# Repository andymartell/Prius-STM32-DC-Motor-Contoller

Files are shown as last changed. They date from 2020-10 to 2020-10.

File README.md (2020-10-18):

# Prius-STM32-DC-Motor-Contoller

18/10/20  Updated the following:

- corrected tracking error around MG1 and MG2 current sensors.  J7 footprint updated (J1 left unchanged as tracking layout is currently ok).
- updated file names to remove spaces
- removed SG3204 and TX4313 -5V charge pumps and added LM2776 in their place in line with Jack Bauers latest updates

17/10/20  Initial release of files for manufacture.  
There are issues with these files, so use at your own risk.  
An updated version will follow once initial testing is complete!

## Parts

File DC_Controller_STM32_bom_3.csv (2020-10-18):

Component | Description | Part | References | Value | Footprint | Quantity Per PCB | Datasheet | JLPCB Component | JLPCB Extended | Mouser Part Number | Manufacturer_Name | Height | Mouser Price/Stock | Manufacturer_Part_Number | Arrow Part Number
1 | Unpolarized capacitor | C | C6 C7 C8 C11 C13 C16 C17 C18 C19 C25 C28 C32 C33 C34 C37 C38 C39 C41 C44 C45 C46 C47 C48 | 100nF | C_0603_1608Metric | 23 | ~ | C14663
2 | Unpolarized capacitor | C | C23 | 100uF | CP_EIA-3528-21_Kemet-B | 1 | ~ | C16133
3 | Polarized capacitor | CP | C61 C63 C64 C65 | 100uF | CP_EIA-3528-21_Kemet-B | 4 | ~ | C16133
4 | Unpolarized capacitor | C | C57 C75 C77 | 10uF | C_0805_2012Metric | 3 | ~ | C15850
5 | Unpolarized capacitor | C | C62 | 1n5 | C_0805_2012Metric | 1 | ~ | C1717
6 | Unpolarized capacitor | C | C9 C14 C20 C69 C70 C71 C72 | 1nF | C_0603_1608Metric | 7 | ~ | C1588
7 | Unpolarized capacitor | C | C1 C2 C4 C5 C10 C21 C26 C29 C30 C49 C54 C58 C67 C68 C76 | 1uF | C_0603_1608Metric | 15 | ~ | C15849
8 | Unpolarized capacitor | C | C74 | 1uF | C_0805_2012Metric | 1 | ~ | C15849
9 | Unpolarized capacitor | C | C12 C15 C35 C36 C40 C42 C43 | 20pF | C_0603_1608Metric | 7 | ~ | C1648
10 | Unpolarized capacitor | C | C27 C31 C53 | 22nf | C_0603_1608Metric | 3 | ~ | C21122
11 | Unpolarized capacitor | C | C59 | 22uF | C_0805_2012Metric | 1 | ~ | C45783
12 | Polarized capacitor | CP | C60 C66 | 330uF | CP_Elec_10x10 | 2 | ~ | C134522 | e
13 | Unpolarized capacitor | C | C55 | 33pF | C_0603_1608Metric | 1 | ~ | C1663
14 | Unpolarized capacitor | C | C3 C56 C73 | 4.7uF | C_0805_2012Metric | 3 | ~ | C1779
15 | Unpolarized capacitor | C | C22 C24 | 47n | C_0603_1608Metric | 2 | ~ | C1622
16 | 75V 0.15A Fast Switching Diode, SOD-123 | 1N4148W | D2 D5 D6 D7 D8 D9 D10 | 1N4148WS | D_SOD-323 | 7 | https://www.vishay.com/docs/85748/1n4148w.pdf | C2128
17 | Light emitting diode | LED | D1 D3 D4 D14 | LED | LED_0805_2012Metric | 4 | ~ | C84256
18 | Diode | D | D11 | SS54B | D_SMA | 1 | ~ | C22452
19 | Schottky diode | D_Schottky | D12 D13 | SS54B | D_SMA | 2 | ~ | C22452
20 | JST (JAPAN SOLDERLESS TERMINALS) - BM02B-CPTK-1A-TB - CONNECTOR, HEADER, 2POS, 1ROW, 2MM | BM02B-CPTK-1A-TB | J5 | BM02B-CPTK-1A-TB | BM02BCPTK1ATB | 1 | http://www.jst-mfg.com/product/pdf/eng/eCPT.pdf |  |  | 306-BM02B-CPTK-1A-TB | JST (JAPAN SOLDERLESS TERMINALS) | 11.7 | https://www.mouser.co.uk/ProductDetail/JST-Automotive/BM02B-CPTK-1A-TB?qs=XoGB3caz5%2FYlNzGrdhaY5g%3D%3D | BM02B-CPTK-1A-TB
21 | Header Top 8 Double CPT | BM08B-CPTK-1A-TB | J8 | BM08B-CPTK-1A-TB | BM08BCPTK1ATB | 1 | http://www.jst-mfg.com/product/pdf/eng/eCPT.pdf |  |  | 306-BM08B-CPTK-1A-TB | JST (JAPAN SOLDERLESS TERMINALS) | 12 | https://www.mouser.co.uk/ProductDetail/JST-Automotive/BM08B-CPTK-1A-TB?qs=XoGB3caz5%2FYvSzPNYjsAKw%3D%3D | BM08B-CPTK-1A-TB
22 | Top Entry disconnectable, crimp style Shrouded Header, 50 positions | BM50B-SHLDS-G-TFT | J6 | BM50B-SHLDS-G-TFT | BM50BSHLDSGTFT | 1 | http://www.jst-mfg.com/product/pdf/eng/eSHLD.pdf |  |  |  | JST (JAPAN SOLDERLESS TERMINALS) | 4.05 |  | BM50B-SHLDS-G-TFT
23 | Generic connector, single row, 01x02, script generated (kicad-library-utils/schlib/autogen/connector/) | Conn_01x02 | J13 J19 | Conn_01x02 | PinHeader_1x02_P2.54mm_Vertical | 2 | ~
24 | Generic connector, single row, 01x03, script generated (kicad-library-utils/schlib/autogen/connector/) | Conn_01x03 | J12 | Conn_01x03 | PinHeader_1x03_P2.54mm_Vertical | 1 | ~
25 | Generic connector, single row, 01x04, script generated (kicad-library-utils/schlib/autogen/connector/) | Conn_01x04 | J4 J10 J17 | Conn_01x04 | PinHeader_1x04_P2.54mm_Vertical | 3 | ~
26 | Generic connector, single row, 01x06, script generated (kicad-library-utils/schlib/autogen/connector/) | Conn_01x06 | J15 | Conn_01x06 | PinHeader_1x06_P2.54mm_Vertical | 1 | ~
27 | Generic connector, double row, 02x05, odd/even pin numbering scheme (row 1 odd numbers, row 2 even numbers), script generated (kicad-library-utils/schlib/autogen/connector/) | Conn_02x05_Odd_Even | J14 | Conn_02x05_Odd_Even | PinHeader_2x05_P2.54mm_Vertical | 1 | ~
28 | Generic connector, double row, 02x05, odd/even pin numbering scheme (row 1 odd numbers, row 2 even numbers), script generated (kicad-library-utils/schlib/autogen/connector/) | Conn_02x05_Odd_Even | J9 | Conn_02x05_Odd_Even | PinHeader_2x05_P2.54mm_Horizontal | 1 | ~
29 | Generic connector, double row, 02x06, odd/even pin numbering scheme (row 1 odd numbers, row 2 even numbers), script generated (kicad-library-utils/schlib/autogen/connector/) | Conn_02x06_Odd_Even | J11 | Conn_02x06_Odd_Even | PinHeader_2x06_P2.54mm_Vertical | 1 | ~
30 | Generic connector, double row, 02x20, odd/even pin numbering scheme (row 1 odd numbers, row 2 even numbers), script generated (kicad-library-utils/schlib/autogen/connector/) | Conn_02x20_Odd_Even | J2 | Conn_02x20_Odd_Even | IDC-Header_2x20_P2.54mm_Horizontal | 1 | ~
31 | JST (JAPAN SOLDERLESS TERMINALS) - SM02B-CPTK-1A-TB - CONNECTOR, HEADER, 2POS, 1ROW, 2MM | SM02B-CPTK-1A-TB | J3 | SM02B-CPTK-1A-TB | SM02BCPTK1ATB | 1 | https://www.jst.co.uk/downloads/series/eCPT_(15-08-31).pdf |  |  | 306-SM02B-CPTK-1A-TB | JST (JAPAN SOLDERLESS TERMINALS) | 6.8 | https://www.mouser.co.uk/ProductDetail/JST-Automotive/SM02B-CPTK-1A-TB?qs=XoGB3caz5%2FZTJkgXMJqmuw%3D%3D | SM02B-CPTK-1A-TB
32 | Automotive Connectors SIDE ENTRY CPT HDR 2.0MM PITCH | SM08B-CPTK-1A-TBL | J7 | SM08B-CPTK-1A-TB | SM08BCPTK1ATBL_odd_even | 1 | http://www.jst-mfg.com/product/pdf/eng/eCPT.pdf |  |  |  | JST (JAPAN SOLDERLESS TERMINALS) | 12 |  | SM08B-CPTK-1A-TB
33 | Automotive Connectors SIDE ENTRY CPT HDR 2.0MM PITCH | SM08B-CPTK-1A-TBL | J1 | SM08B-CPTK-1A-TBL | SM08BCPTK1ATBL | 1 | http://www.jst-mfg.com/product/pdf/eng/eCPT.pdf |  |  | 306-SM08B-CPTK-1ATBL | JST (JAPAN SOLDERLESS TERMINALS) | 9.3 | https://www.mouser.co.uk/ProductDetail/JST-Automotive/SM08B-CPTK-1A-TBL?qs=XoGB3caz5%2FYptClYcBhvSw%3D%3D | SM08B-CPTK-1A-TBL
34 | CABLE TAG-CONNECT IN-CIRCUIT LEG | TC2030-MCP | J16 J18 | TC2030-MCP | TC2030MCP | 2 | http://www.tag-connect.com/Materials/TC2030-MCP%20Datasheet.pdf |  |  |  | Tag Connect | 18.669 |  | TC2030-MCP | TC2030-MCP
35 | Inductor, small symbol | L_Small | L2 L3 | 10uH | L_0805_2012Metric | 2 | ~ | C1046 | e
36 | Inductor | L | L4 | 220uH | L_12x12mm_H6mm | 1 | ~ | C169402 | e
37 | Inductor | L | L1 | 4.7uH | L_1210_3225Metric | 1 | ~ | C76842 | e
38 | 0.2A Ic, 40V Vce, Small Signal NPN Transistor, SOT-23 | MMBT3904 | Q2 Q10 Q11 Q12 Q13 Q14 Q15 Q16 Q17 Q18 Q19 Q20 Q21 Q22 Q23 Q24 Q25 | MMBT3904 | SOT-23 | 17 | https://www.fairchildsemi.com/datasheets/2N/2N3904.pdf | C20526
39 | N-MOSFET transistor, gate/drain/source, drain connected to mounting plane | Q_NMOS_GDSD | Q1 Q5 Q6 Q7 Q8 Q9 | NCV8402A | SOT-223 | 6 | ~ | C77755 | e
40 | NPN transistor, base/emitter/collector | Q_NPN_BEC | Q3 Q4 | S8050 | SOT-23 | 2 | ~ | C2146
41 | Resistor | R | R103 | 0.22R | R_0805_2012Metric | 1 | ~ | C36234 | e
42 | Resistor | R | R12 R15 R17 R93 R98 R106 R107 R121 R125 | 0R | R_0603_1608Metric | 9 | ~ | C21189
43 | Resistor | R | R37 | 1.2k | R_0603_1608Metric | 1 | ~ | C22765
44 | Resistor | R | R10 R11 R16 R19 R30 R109 R112 | 1.5k | R_0603_1608Metric | 7 | ~ | C22843
45 | Resistor | R | R54 R57 R58 R61 R62 R64 R66 R68 R70 R72 R74 R76 R78 R80 | 100R | R_0603_1608Metric | 14 | ~ | C22775
46 | Resistor | R | R87 R88 R89 R101 | 100k | R_0603_1608Metric | 4 | ~ | C25803
47 | Resistor | R | R2 R7 R22 R23 R29 R32 R35 R38 R39 R41 R43 R52 R81 R91 R97 | 10k | R_0603_1608Metric | 15 | ~ | C25804
48 | Resistor | R | R83 | 120R | R_0603_1608Metric | 1 | ~ | C22787
49 | Resistor | R | R102 | 180R | R_0603_1608Metric | 1 | ~ | C22828
50 | Resistor | R | R26 | 182k | R_0805_2012Metric | 1 | ~
51 | Resistor | R | R21 R42 R44 R46 R49 R50 R53 R55 R56 R59 R60 R63 R65 R67 R69 R71 R73 R75 R77 R79 R82 R84 R85 R92 R96 R126 | 1k | R_0603_1608Metric | 26 | ~ | C21190
52 | Resistor | R | R5 R40 R48 | 2.2k | R_0603_1608Metric | 3 | ~ | C4190
53 | Resistor | R | R105 | 2.4k | R_0603_1608Metric | 1 | ~ | C22940
54 | Resistor | R | R108 | 2.7k | R_0603_1608Metric | 1 | ~ | C13167
55 | Resistor | R | R45 R47 R110 | 22k | R_0603_1608Metric | 3 | ~ | C31850
56 | Resistor | R | R34 R36 | 3.3k | R_0603_1608Metric | 2 | ~ | C22978
57 | Resistor | R | R117 R118 R119 R120 | 3.6k | R_0603_1608Metric | 4 | ~ | C22980
58 | Resistor | R | R31 | 3.9k | R_0603_1608Metric | 1 | ~ | C23018
59 | Resistor | R | R95 | 330R | R_0603_1608Metric | 1 | ~ | C23138
60 | Resistor | R | R27 | 392k | R_0805_2012Metric | 1 | ~
61 | Resistor | R | R3 R4 R13 R14 R111 | 4.7k | R_0603_1608Metric | 5 | ~ | C23162
62 | Resistor | R | R100 | 43k | R_0603_1608Metric | 1 | ~ | C23172
63 | Resistor | R | R1 R8 R9 R130 | 470R | R_0603_1608Metric | 4 | ~ | C23179
64 | Resistor | R | R6 R18 R24 R104 | 47k | R_0603_1608Metric | 4 | ~ | C25819
65 | Resistor | R | R28 R33 R51 R90 | 5.1k | R_0603_1608Metric | 4 | ~ | C23186
66 | Resistor | R | R86 | 560R | R_0603_1608Metric | 1 | ~ | C23204
67 | Resistor | R | R113 R114 R115 R116 | 6.2k | R_0603_1608Metric | 4 | ~ | C4260
68 | Resistor | R | R94 | 680R | R_0603_1608Metric | 1 | ~ | C23228
69 | Resistor | R | R99 | 8.2k | R_0603_1608Metric | 1 | ~ | C25981
70 | Resistor | R | R25 | 976k | R_0805_2012Metric | 1 | ~
71 | Resistor | R | R20 R122 R123 R124 R129 | NF | R_0603_1608Metric | 5 | ~ | C21189
72 | Resistor | R | R127 R128 | NF 56k | R_0603_1608Metric | 2 | ~ | C23206
73 | Push button switch, generic, two pins | SW_Push | SW1 | SW_Push | Panasonic_EVQPUK_EVQPUB | 1 | ~
74 | SPDT Analog Swich, Low-Voltage CMOS | 74LVC1G3157 | U2 U5 | 74LVC1G3157GW | SOT-363_SC-70-6 | 2 | http://www.ti.com/lit/sg/scyt129e/scyt129e.pdf | C265126 | e
75 | 20MHz, 32kB Flash, 2kB SRAM, 1kB EEPROM, TQFP-32 | ATmega328P-AU | U9 | ATmega328P-AU | TQFP-32_7x7mm_P0.8mm | 1 | http://ww1.microchip.com/downloads/en/DeviceDoc/ATmega328_P%20AVR%20MCU%20with%20picoPower%20Technology%20Data%20Sheet%2040001984A.pdf | C14877
76 | Switched capacitor inverter, inverts positive voltage +2.7 to +5.5V to negative, 200mA, SOT-23-6 | LM2776 | U10 | LM2776 | SOT-23-6 | 1 | http://www.ti.com/lit/ds/symlink/lm2776.pdf | C69527 | e
77 | TimerBlox Monostable Pulse Generator (One Shot), Rising-edge input, non-retriggerable, TSOT-23-6 | LTC6993xS6-1 | U7 | LTC6992CS6-1 | TSOT-23-6 | 1 | https://www.analog.com/media/en/technical-documentation/data-sheets/69931234fc.pdf | C117381 | e
78 |  | MAX889RESA+ | U15 | MAX889RESA+ | SOIC-8_3.9x4.9mm_P1.27mm | 1
79 | 1.5A, step-up/down/inverting switching regulator, 3-40V Vin, 100kHz, SO-8 | MC34063AD | U13 | MC34063ABD-TR | SOIC-8_3.9x4.9mm_P1.27mm | 1 | http://www.onsemi.com/pub_link/Collateral/MC34063A-D.PDF | C81155 | e
80 | Stand-Alone CAN Controller with SPI Interface, SOIC-18 | MCP2515-xSO | U6 | MCP2515-I/SO | SOIC-18W_7.5x11.6mm_P1.27mm | 1 | http://ww1.microchip.com/downloads/en/DeviceDoc/21801e.pdf | C12368
81 | 1.8V Low-Power Push-Pull Output Comparator, SC-70-5 | MCP6561x-LT | U1 | MCP6561x-LT | SOT-353_SC-70-5 | 1 | http://ww1.microchip.com/downloads/en/DeviceDoc/22139C.pdf | C144221 | e
82 |  | MP2451 | U11 | MP2359 | TSOT-23-6 | 1 |  | C14259
83 | CAN Bus Transceivers, 3.3V, 1Mbps, Low-Power capabilities, SOIC | SN65HVD230 | U4 | SN65HVD230 | SOIC-8_3.9x4.9mm_P1.27mm | 1 | http://www.ti.com/lit/ds/symlink/sn65hvd230.pdf | C12084
84 | ARM Cortex-M3 MCU, 128KB flash, 64KB RAM, 72MHz, 2-3.6V, 51 GPIO, LQFP-64 | STM32F105RBTx | U3 | STM32F103RBT6 | LQFP-64_10x10mm_P0.5mm | 1 | http://www.st.com/st-web-ui/static/active/en/resource/technical/document/datasheet/CD00220364.pdf | C8735
85 | High-Speed CAN Transceiver, silent mode, SOIC-8 | TJA1051T | U8 | TJA1050T | SOIC-8_3.9x4.9mm_P1.27mm | 1 | http://www.nxp.com/documents/data_sheet/TJA1051.pdf | C6952
86 | Positive 60-250mA Low Dropout Regulator, Fixed Output, SOT-23 | XC6206PxxxMR | U12 | XC6206P332MR | SOT-23 | 1 | https://www.torexsemi.com/file/xc6206/XC6206.pdf | C5446
87 | Four pin crystal, GND on pins 2 and 4 | Crystal_GND24 | Y1 Y3 | 16MHz | Crystal_SMD_3225-4Pin_3.2x2.5mm | 2 | ~ | C13738
88 | Two pin crystal | Crystal | Y2 | 8M0 | Crystal_SMD_5032-2Pin_5.0x3.2mm | 1 | ~ | C115962
Component Groups: | 88
Component Count: | 284
Fitted Components: | 284
Number of PCBs: | 1
Total components: | 284
Schematic Version: | 3
Schematic Date: | 2020-10-18
PCB Variant: | [u'default']
BoM Date: | 18/10/2020 10:13:55
Schematic Source: | C:\Users\andym\OneDrive\10 Documents\01 Projects\01 Electric Car\280 Prius DC Motor Contoller PCB\10 Kicad\10 DC Controller STM32 V2\DC_Controller_STM32.sch
KiCad Version: | Eeschema (5.1.5)-3

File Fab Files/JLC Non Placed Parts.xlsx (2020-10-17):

References | Value | Footprint | Quantity |  | Mouser Order Number | MOQ | RS Order Number | MOQ | Farnell Order Number
J5 | BM02B-CPTK-1A-TB | BM02BCPTK1ATB | 1 |  | 306-BM02B-CPTK-1A-TB | 1 | 123-8258 | 5
J8 | BM08B-CPTK-1A-TB | BM08BCPTK1ATB | 1 |  | 306-BM08B-CPTK-1A-TB | 1 |  |  | 2708676
J3 | SM02B-CPTK-1A-TB | SM02BCPTK1ATB | 1 |  | 306-SM02B-CPTK-1A-TB | 1 |  |  | 2708677
SW1 | SW_PUSH | PANASONIC_EVQPUK_EVQPUB | 1 |  | 667-EVQ-PUK02K | 1
U15 | MAX889RESA+ | SOIC-8_3.9X4.9MM_P1.27MM | 1 |  | 700-MAX889RESA | 1
R26 | 182K | R_0805_2012METRIC | 1
J7 | SM08B-CPTK-1A-TB | SM08BCPTK1ATBL | 1 |  | 306-SM08B-CPTK-1ATBL | 2 |  |  | 2708679
J6 | BM50B-SHLDS-G-TFT | BM50BSHLDSGTFT | 1
R27 | 392K | R_0805_2012METRIC | 1
R20,R122,R123,R124 | NF | R_0603_1608METRIC | 4
J1 | SM08B-CPTK-1A-TBL | SM08BCPTK1ATBL | 1 |  |  |  |  |  | 2708679
R25 | 976K | R_0805_2012METRIC | 1
U10 | SGM3204 | SOT-23-6 | 1
U7 | LTC6992CS6-1 | TSOT-23-6 | 1 |  | 584-C6992CS6-1TRMPBF | 1
J4,J10,J17 | CONN_01X04 | PINHEADER_1X04_P2.54MM_VERTICAL | 0
J13,J19 | CONN_01X02 | PINHEADER_1X02_P2.54MM_VERTICAL | 0
J2 | CONN_02X20_ODD_EVEN | IDC-HEADER_2X20_P2.54MM_HORIZONTAL | 0 | RA 20 Way | 517-30340-5002 | 2
J12 | CONN_01X03 | PINHEADER_1X03_P2.54MM_VERTICAL | 0
J11 | CONN_02X06_ODD_EVEN | PINHEADER_2X06_P2.54MM_VERTICAL | 0
J14 | CONN_02X05_ODD_EVEN | PINHEADER_2X05_P2.54MM_VERTICAL | 0
J15 | CONN_01X06 | PINHEADER_1X06_P2.54MM_VERTICAL | 0
J16,J18 | TC2030-MCP | TC2030MCP | 0 |  |  |  | Tag Connect
J9 | CONN_02X05_ODD_EVEN | PINHEADER_2X05_P2.54MM_HORIZONTAL | 0
 |  |  |  |  | 594-D680J25SL0L6UJ5R | 10
 | Caps |  |  |  | 594-S151K25Y5PP6TK7R | 10
 |  |  |  |  | 594-D271K20Y5PH63L6R | 10
 |  |  |  |  | 594-D471K20Y5PH6UJ5R | 10
 | Tag Connect board |  |  |  | 517-30310-6002 | 3
 |  |  |  |  | 517-30320-6002 | 3

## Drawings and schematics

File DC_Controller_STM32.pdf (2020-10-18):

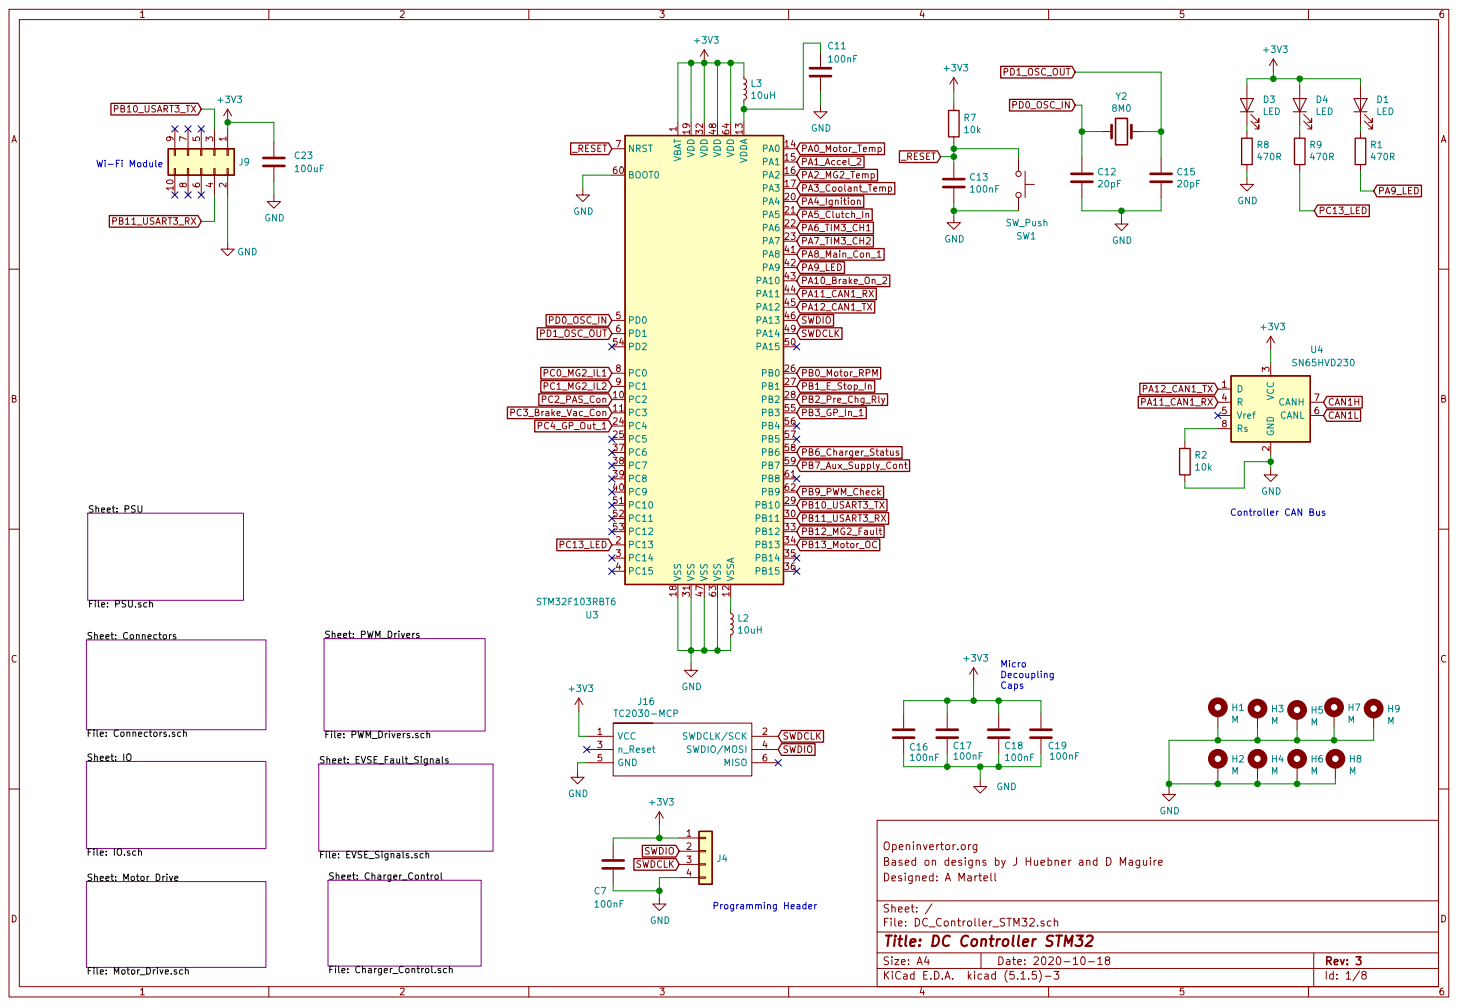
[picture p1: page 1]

1 VDD 19 VDD 32 VDD 48 VDD 64 VDDA 13 VSS 18 VSS 31 VSS 47 VSS 63 VSSA 12 U3 STM32F103RBT6 GND

Controller CAN Bus Programming Header

File: EVSE_Signals.sch Sheet: Connectors File: Connectors.sch Sheet: IO

Based on designs by J Huebner and D Maguire
File: DC_Controller_STM32.sch Sheet: / Designed: A Martell

Id: 1/8 Title: DC Controller STM32

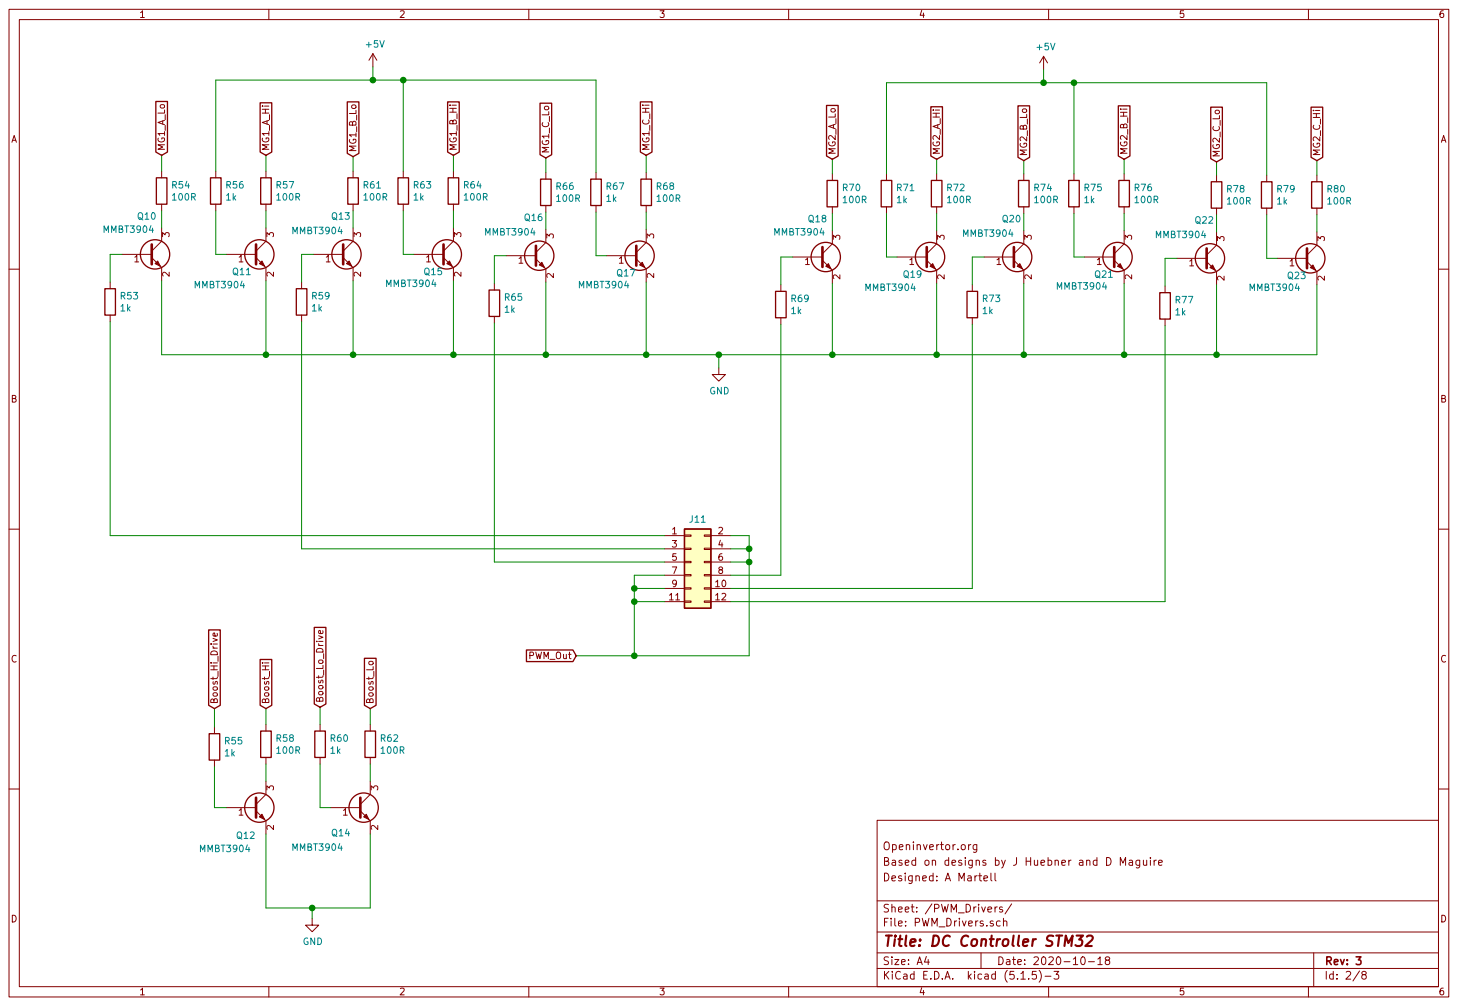
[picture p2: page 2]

9 | 10
11 | 12

Openinvertor.org
Based on designs by J Huebner and D Maguire
Designed: A Martell

Sheet: /PWM_Drivers/
File: PWM_Drivers.sch
Id: 2/8 Title: DC Controller STM32

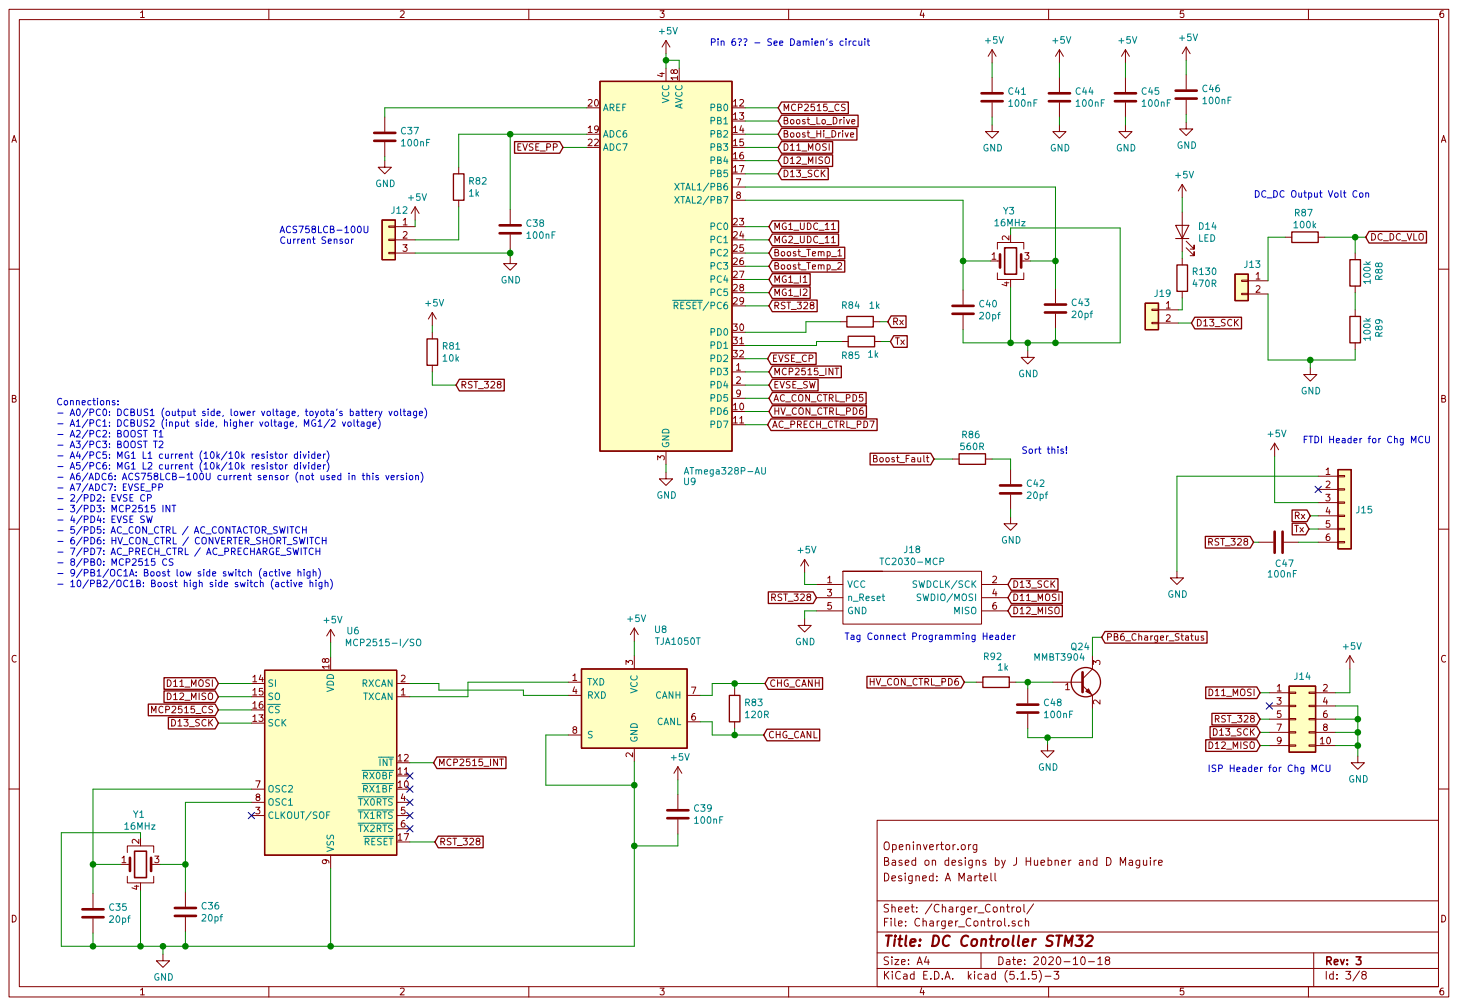
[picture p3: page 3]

Connections: - A0/PC0: DCBUS1 (output side, lower voltage, toyota's battery voltage)

- A1/PC1: DCBUS2 (input side, higher voltage, MG1/2 voltage)
- A2/PC2: BOOST T1
- A3/PC3: BOOST T2
- A4/PC5: MG1 L1 current (10k/10k resistor divider)
- A5/PC6: MG1 L2 current (10k/10k resistor divider)
- A6/ADC6: ACS758LCB-100U current sensor (not used in this version)
- A7/ADC7: EVSE_PP
- 2/PD2: EVSE CP
- 3/PD3: MCP2515 INT
- 4/PD4: EVSE SW
- 5/PD5: AC_CON_CTRL / AC_CONTACTOR_SWITCH
- 6/PD6: HV_CON_CTRL / CONVERTER_SHORT_SWITCH
- 7/PD7: AC_PRECH_CTRL / AC_PRECHARGE_SWITCH
- 8/PB0: MCP2515 CS
- 9/PB1/OC1A: Boost low side switch (active high)
- 10/PB2/OC1B: Boost high side switch (active high)

ISP Header for Chg MCU

Openinvertor.org
Based on designs by J Huebner and D Maguire
Designed: A Martell

Sheet: /Charger_Control/
File: Charger_Control.sch
Id: 3/8 Title: DC Controller STM32

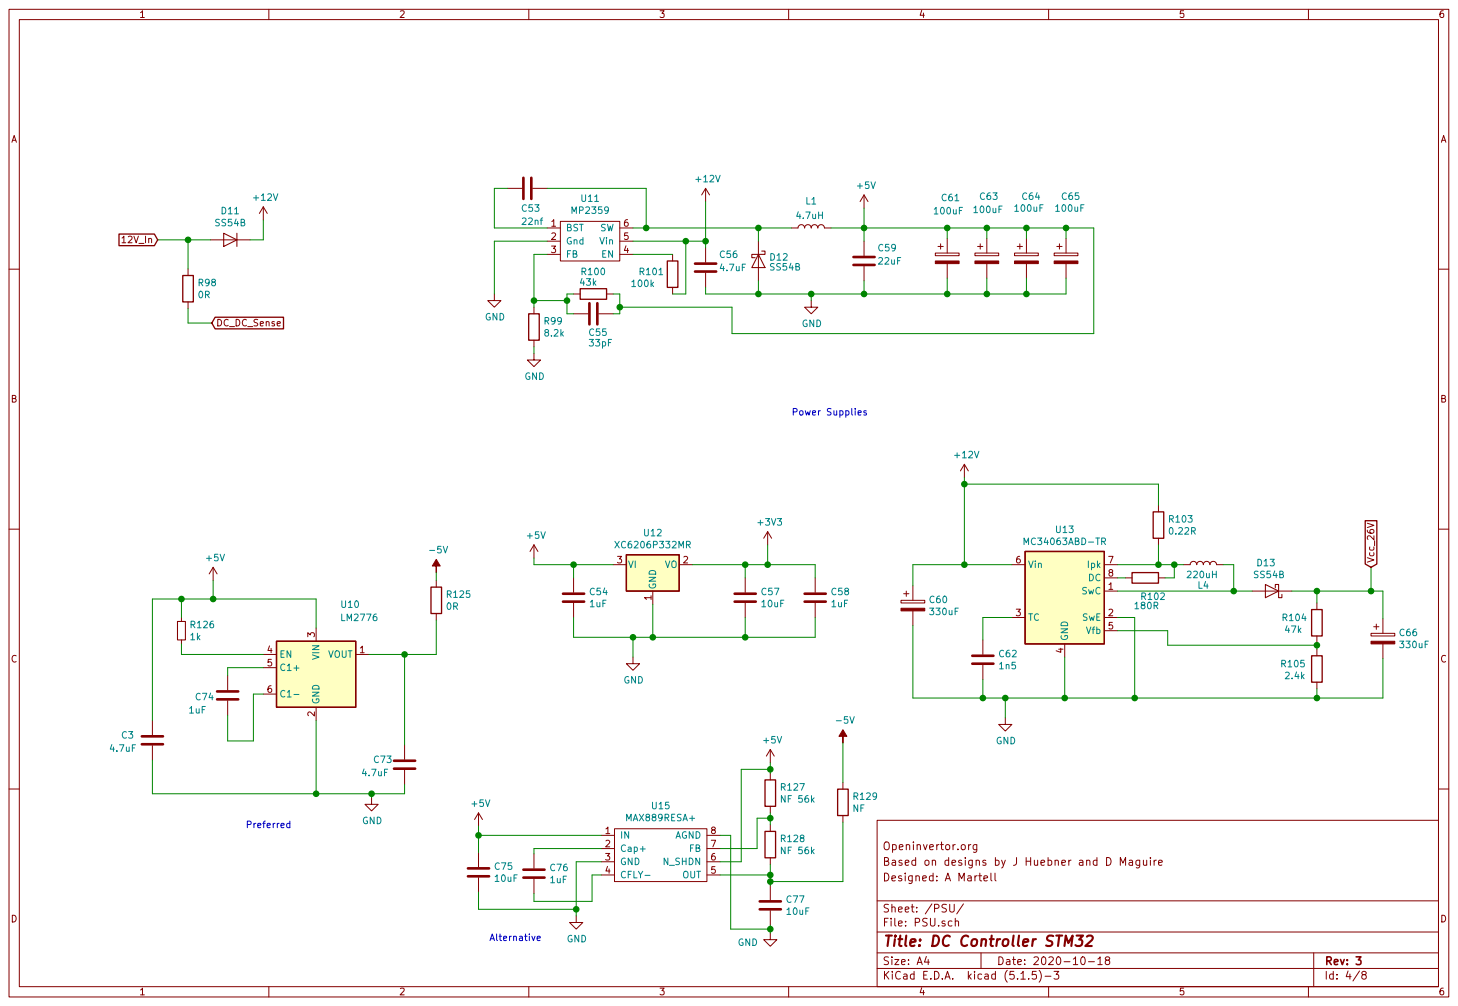
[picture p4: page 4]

Based on designs by J Huebner and D Maguire
File: PSU.sch Sheet: /PSU/ Designed: A Martell

Id: 4/8 Title: DC Controller STM32

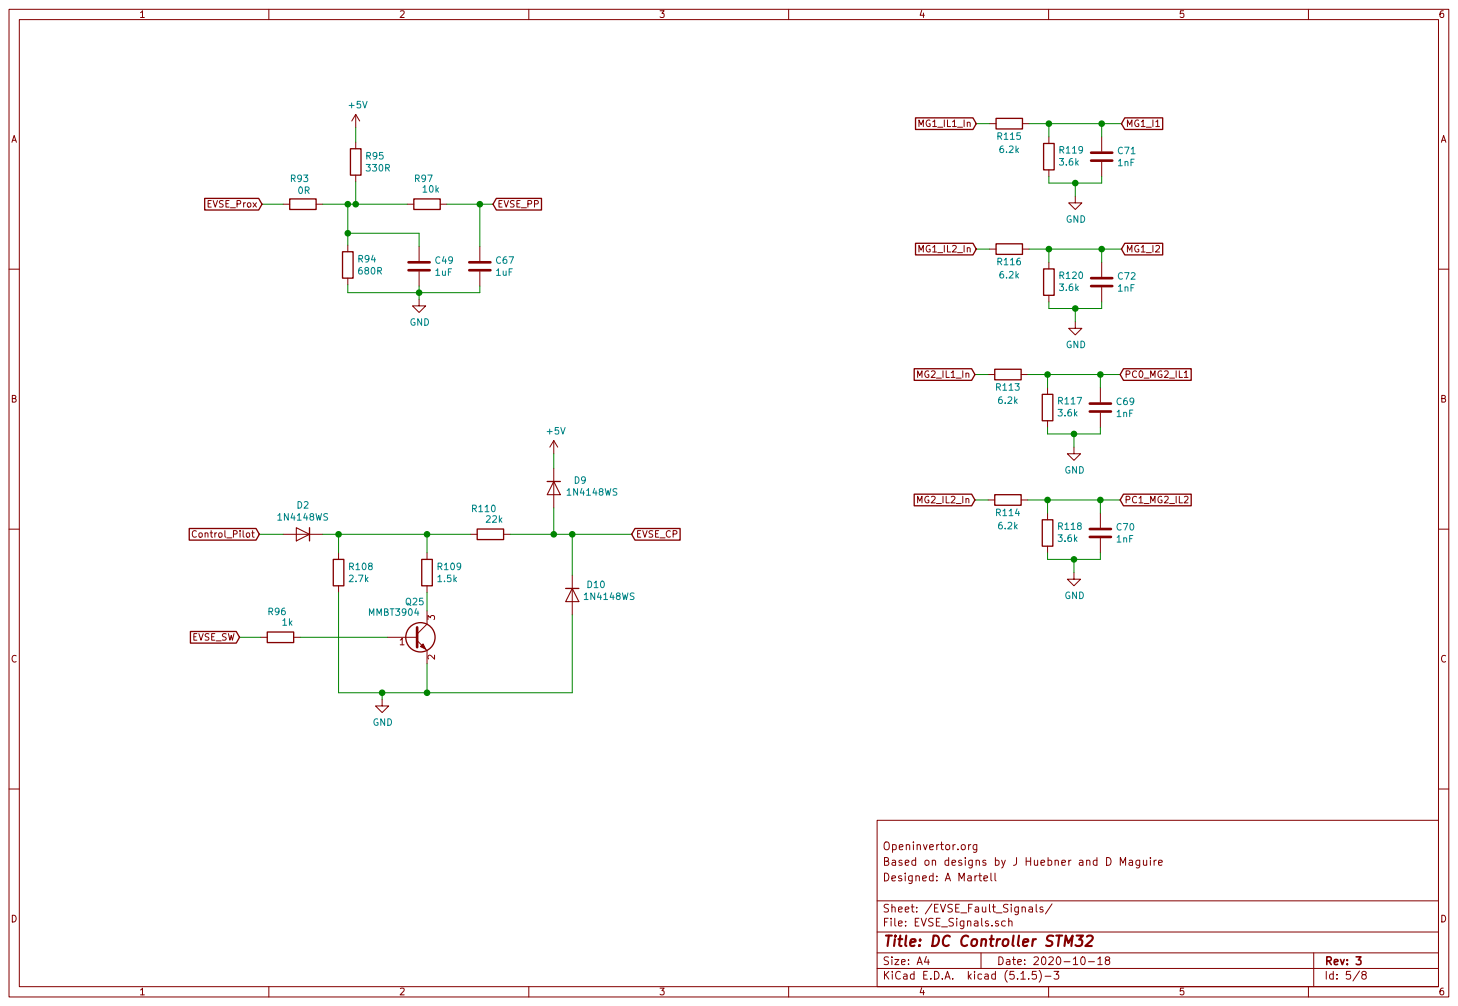
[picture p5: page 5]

Openinvertor.org
Based on designs by J Huebner and D Maguire
Designed: A Martell

Sheet: /EVSE_Fault_Signals/
File: EVSE_Signals.sch
Id: 5/8 Title: DC Controller STM32

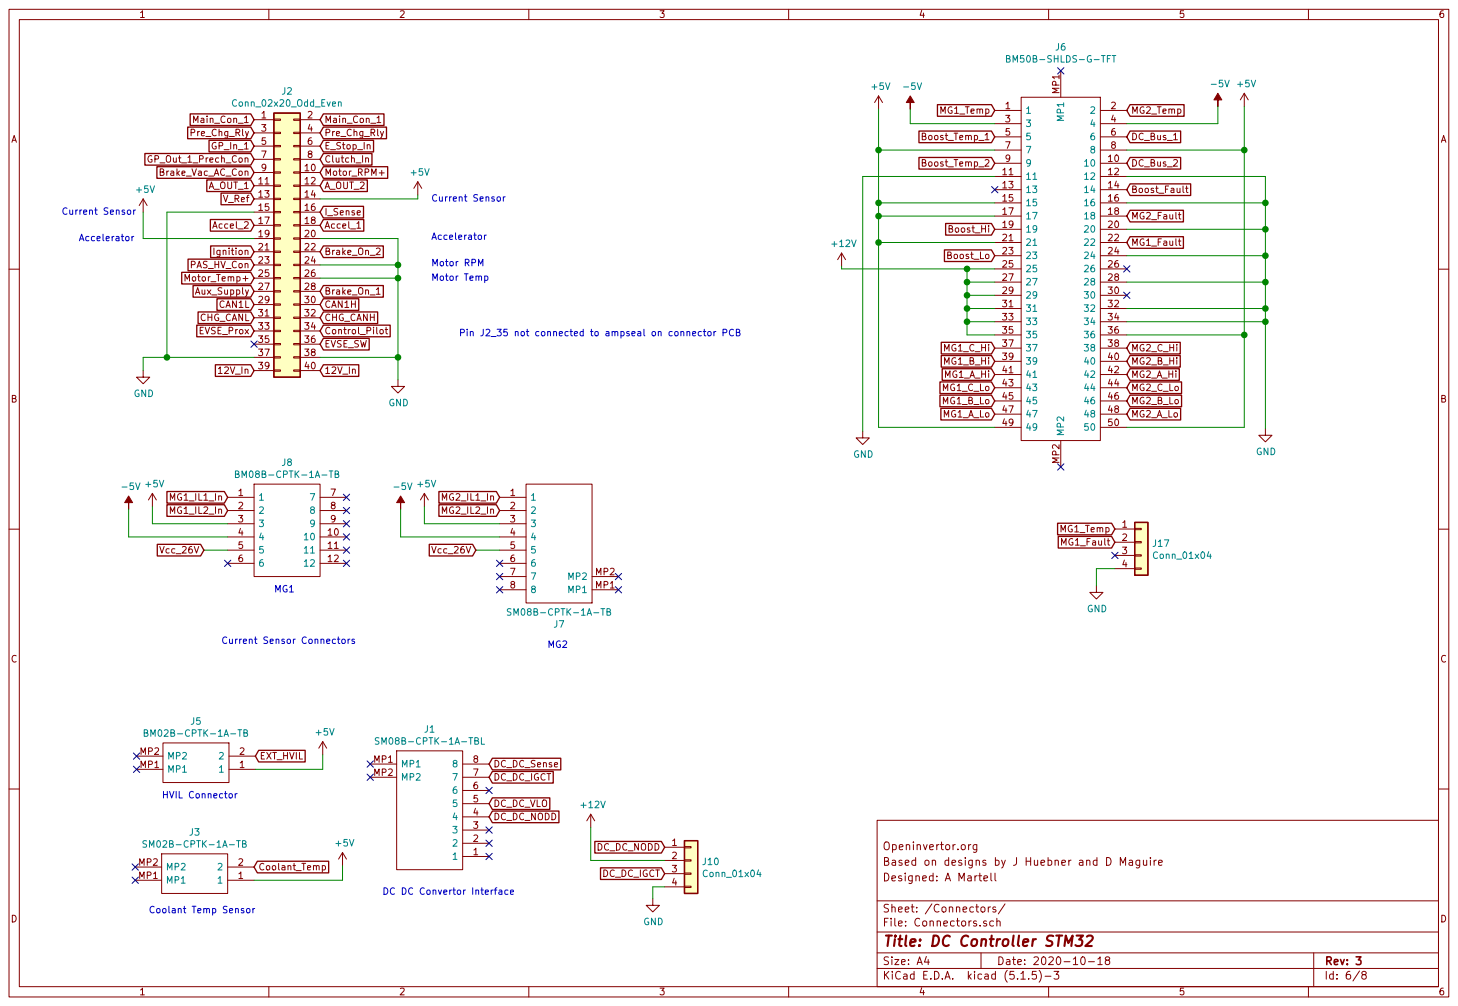
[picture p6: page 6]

Openinvertor.org
Based on designs by J Huebner and D Maguire
File: Connectors.sch Sheet: /Connectors/ Designed: A Martell

Id: 6/8 Title: DC Controller STM32

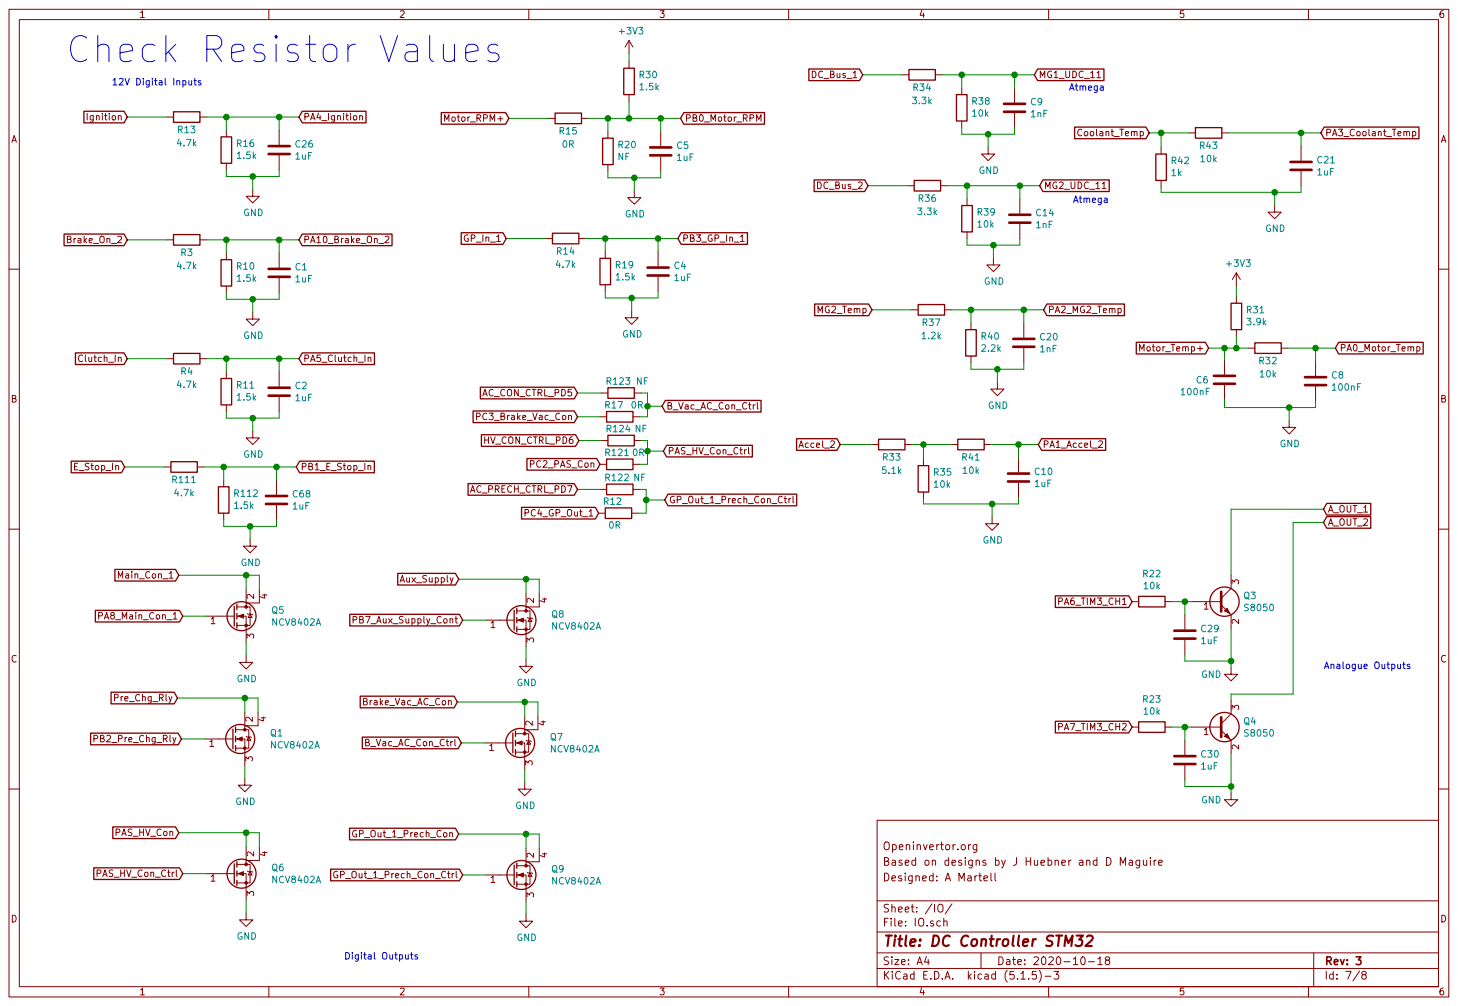
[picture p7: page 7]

Based on designs by J Huebner and D Maguire
File: IO.sch Sheet: /IO/ Designed: A Martell

Id: 7/8 Title: DC Controller STM32

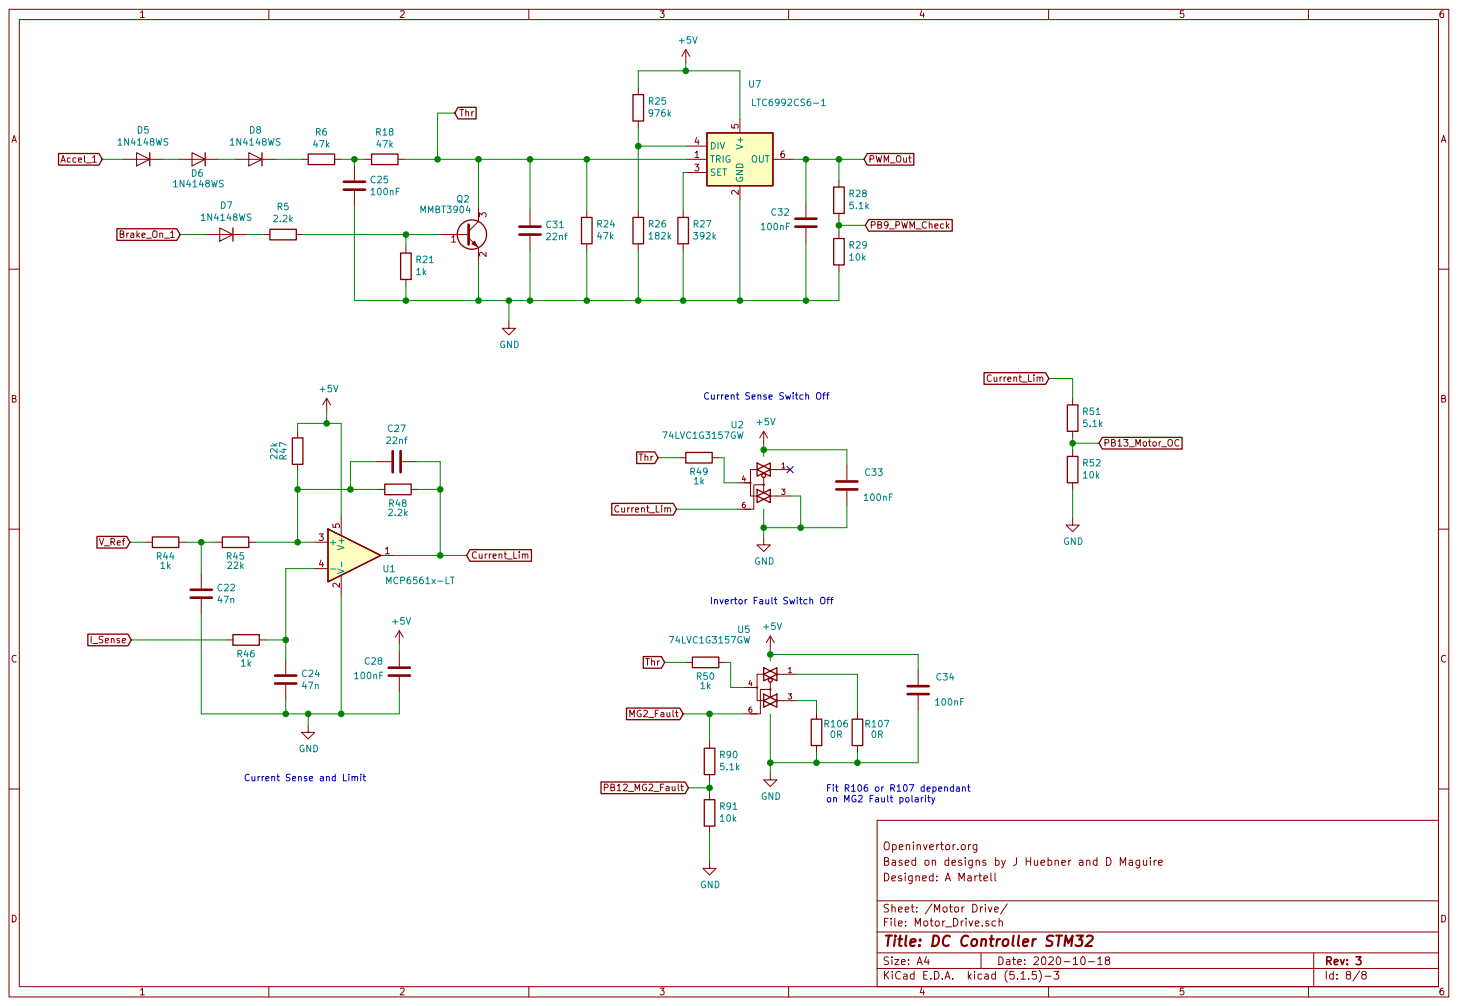
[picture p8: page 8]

2 SET 3 DIV 4 V+
PWM_Out Current Sense Switch Off

Based on designs by J Huebner and D Maguire
File: Motor_Drive.sch Sheet: /Motor Drive/ Designed: A Martell

Id: 8/8 Title: DC Controller STM32

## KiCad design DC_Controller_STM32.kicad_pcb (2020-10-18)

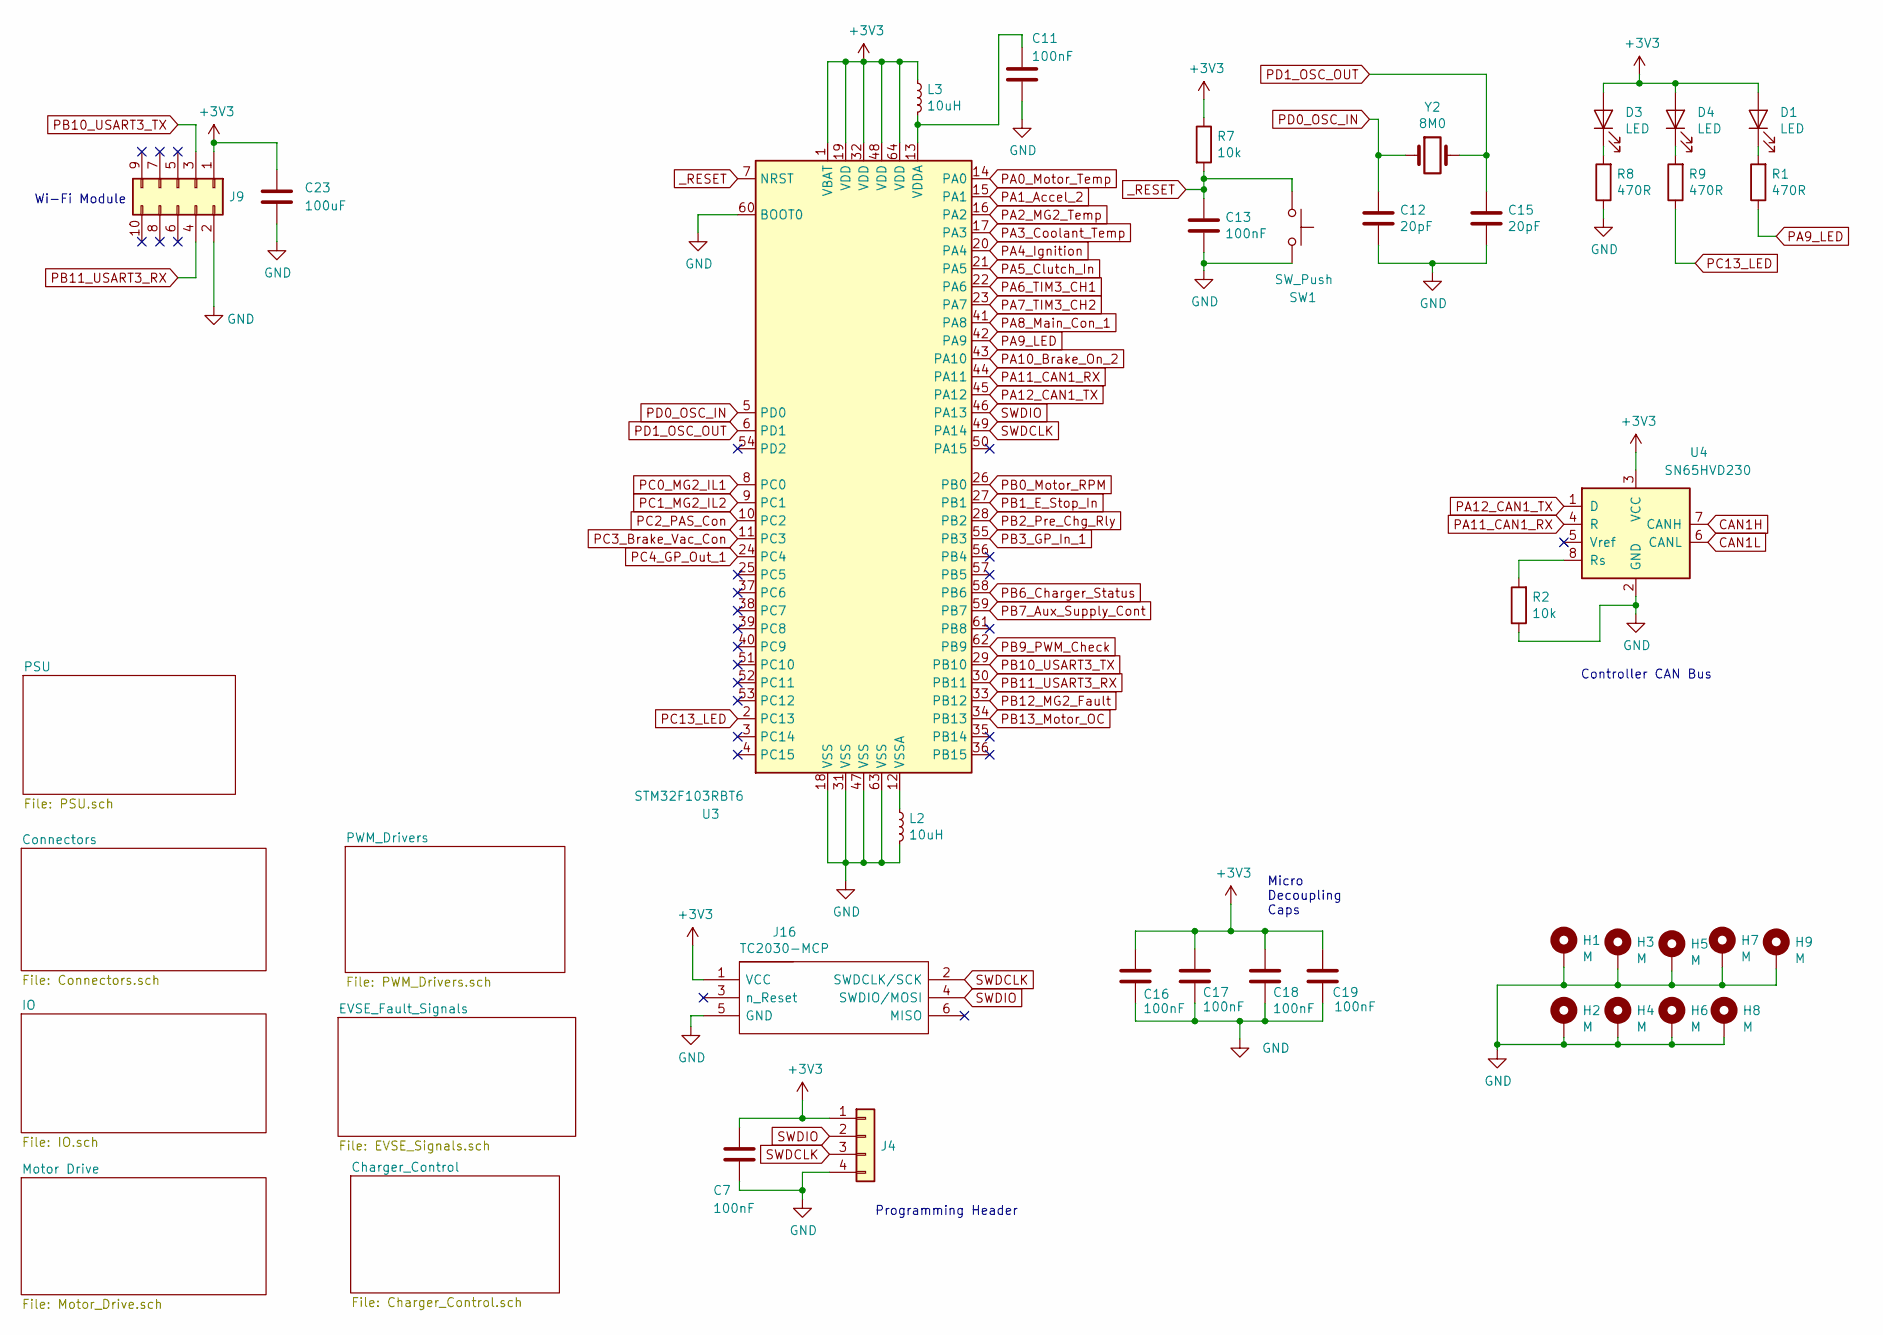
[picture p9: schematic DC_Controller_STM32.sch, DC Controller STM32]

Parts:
C7, C11, C13, C16, C17, C18, C19: 100nF; C_0603_1608Metric
C12, C15: 20pF; C_0603_1608Metric
C23: 100uF; CP_EIA-3528-21_Kemet-B
D1, D3, D4: LED; LED_0805_2012Metric
H1, H2, H3, H4, H5, H6, H7, H8, H9: M; MountingHole_3.2mm_M3_Pad
J4: Conn_01x04; PinHeader_1x04_P2.54mm_Vertical
J9: Conn_02x05_Odd_Even; PinHeader_2x05_P2.54mm_Horizontal
J16: TC2030-MCP; TC2030MCP; Manufacturer_Part_Number TC2030-MCP
L2, L3: 10uH; L_0805_2012Metric
R1, R8, R9: 470R; R_0603_1608Metric
R2, R7: 10k; R_0603_1608Metric
SW1: SW_Push; Panasonic_EVQPUK_EVQPUB
U3: STM32F103RBT6; LQFP-64_10x10mm_P0.5mm
U4: SN65HVD230; SOIC-8_3.9x4.9mm_P1.27mm
Y2: 8M0; Crystal_SMD_5032-2Pin_5.0x3.2mm

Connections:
+3V3: C7.1, C16.1, C17.1, C18.1, C19.1, C23.1, D1.2 (A), D3.2 (A), D4.2 (A), J4.1, J9.1, J16.1 (VCC), L3.1, R7.1, U3.1 (VBAT), U3.19 (VDD), U3.32 (VDD), U3.48 (VDD), U3.64 (VDD), U4.3 (VCC); also elsewhere on the board
CAN1H: U4.7 (CANH); also elsewhere on the board
CAN1L: U4.6 (CANL); also elsewhere on the board
GND: C7.2, C11.2, C12.2, C13.2, C15.2, C16.2, C17.2, C18.2, C19.2, C23.2, H1.1, H2.1, H3.1, H4.1, H5.1, H6.1, H7.1, H8.1, H9.1, J4.4, J9.2, J16.5 (GND), L2.2, R2.1, R8.1, SW1.2, U3.18 (VSS), U3.31 (VSS), U3.47 (VSS), U3.60 (BOOT0), U3.63 (VSS), U4.2 (GND); also elsewhere on the board
unnamed: C11.1, L3.2, U3.13 (VDDA)
unnamed: D1.1 (K), R1.2
unnamed: D3.1 (K), R8.2
unnamed: D4.1 (K), R9.2
unnamed: L2.1, U3.12 (VSSA)
unnamed: R2.2, U4.8 (Rs)
PA0_Motor_Temp: U3.14 (PA0); also elsewhere on the board
PA1_Accel_2: U3.15 (PA1); also elsewhere on the board
PA2_MG2_Temp: U3.16 (PA2); also elsewhere on the board
PA3_Coolant_Temp: U3.17 (PA3); also elsewhere on the board
PA4_Ignition: U3.20 (PA4); also elsewhere on the board
PA5_Clutch_In: U3.21 (PA5); also elsewhere on the board
PA6_TIM3_CH1: U3.22 (PA6); also elsewhere on the board
PA7_TIM3_CH2: U3.23 (PA7); also elsewhere on the board
PA8_Main_Con_1: U3.41 (PA8); also elsewhere on the board
PA9_LED: R1.1, U3.42 (PA9)
PA10_Brake_On_2: U3.43 (PA10); also elsewhere on the board
PA11_CAN1_RX: U3.44 (PA11), U4.4 (R)
PA12_CAN1_TX: U3.45 (PA12), U4.1 (D)
PB0_Motor_RPM: U3.26 (PB0); also elsewhere on the board
PB1_E_Stop_In: U3.27 (PB1); also elsewhere on the board
PB2_Pre_Chg_Rly: U3.28 (PB2); also elsewhere on the board
PB3_GP_In_1: U3.55 (PB3); also elsewhere on the board
PB6_Charger_Status: U3.58 (PB6); also elsewhere on the board
PB7_Aux_Supply_Cont: U3.59 (PB7); also elsewhere on the board
PB9_PWM_Check: U3.62 (PB9); also elsewhere on the board
PB10_USART3_TX: J9.3, U3.29 (PB10)
PB11_USART3_RX: J9.4, U3.30 (PB11)
PB12_MG2_Fault: U3.33 (PB12); also elsewhere on the board
PB13_Motor_OC: U3.34 (PB13); also elsewhere on the board
PC0_MG2_IL1: U3.8 (PC0); also elsewhere on the board
PC1_MG2_IL2: U3.9 (PC1); also elsewhere on the board
PC2_PAS_Con: U3.10 (PC2); also elsewhere on the board
PC3_Brake_Vac_Con: U3.11 (PC3); also elsewhere on the board
PC4_GP_Out_1: U3.24 (PC4); also elsewhere on the board
PC13_LED: R9.1, U3.2 (PC13)
PD0_OSC_IN: C12.1, U3.5 (PD0), Y2.1
PD1_OSC_OUT: C15.1, U3.6 (PD1), Y2.2
SWDCLK: J4.3, J16.2 (SWDCLK/SCK), U3.49 (PA14)
SWDIO: J4.2, J16.4 (SWDIO/MOSI), U3.46 (PA13)
_RESET: C13.1, R7.2, SW1.1, U3.7 (NRST)

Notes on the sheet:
Programming Header
Wi-Fi Module
Micro Decoupling Caps
Controller CAN Bus

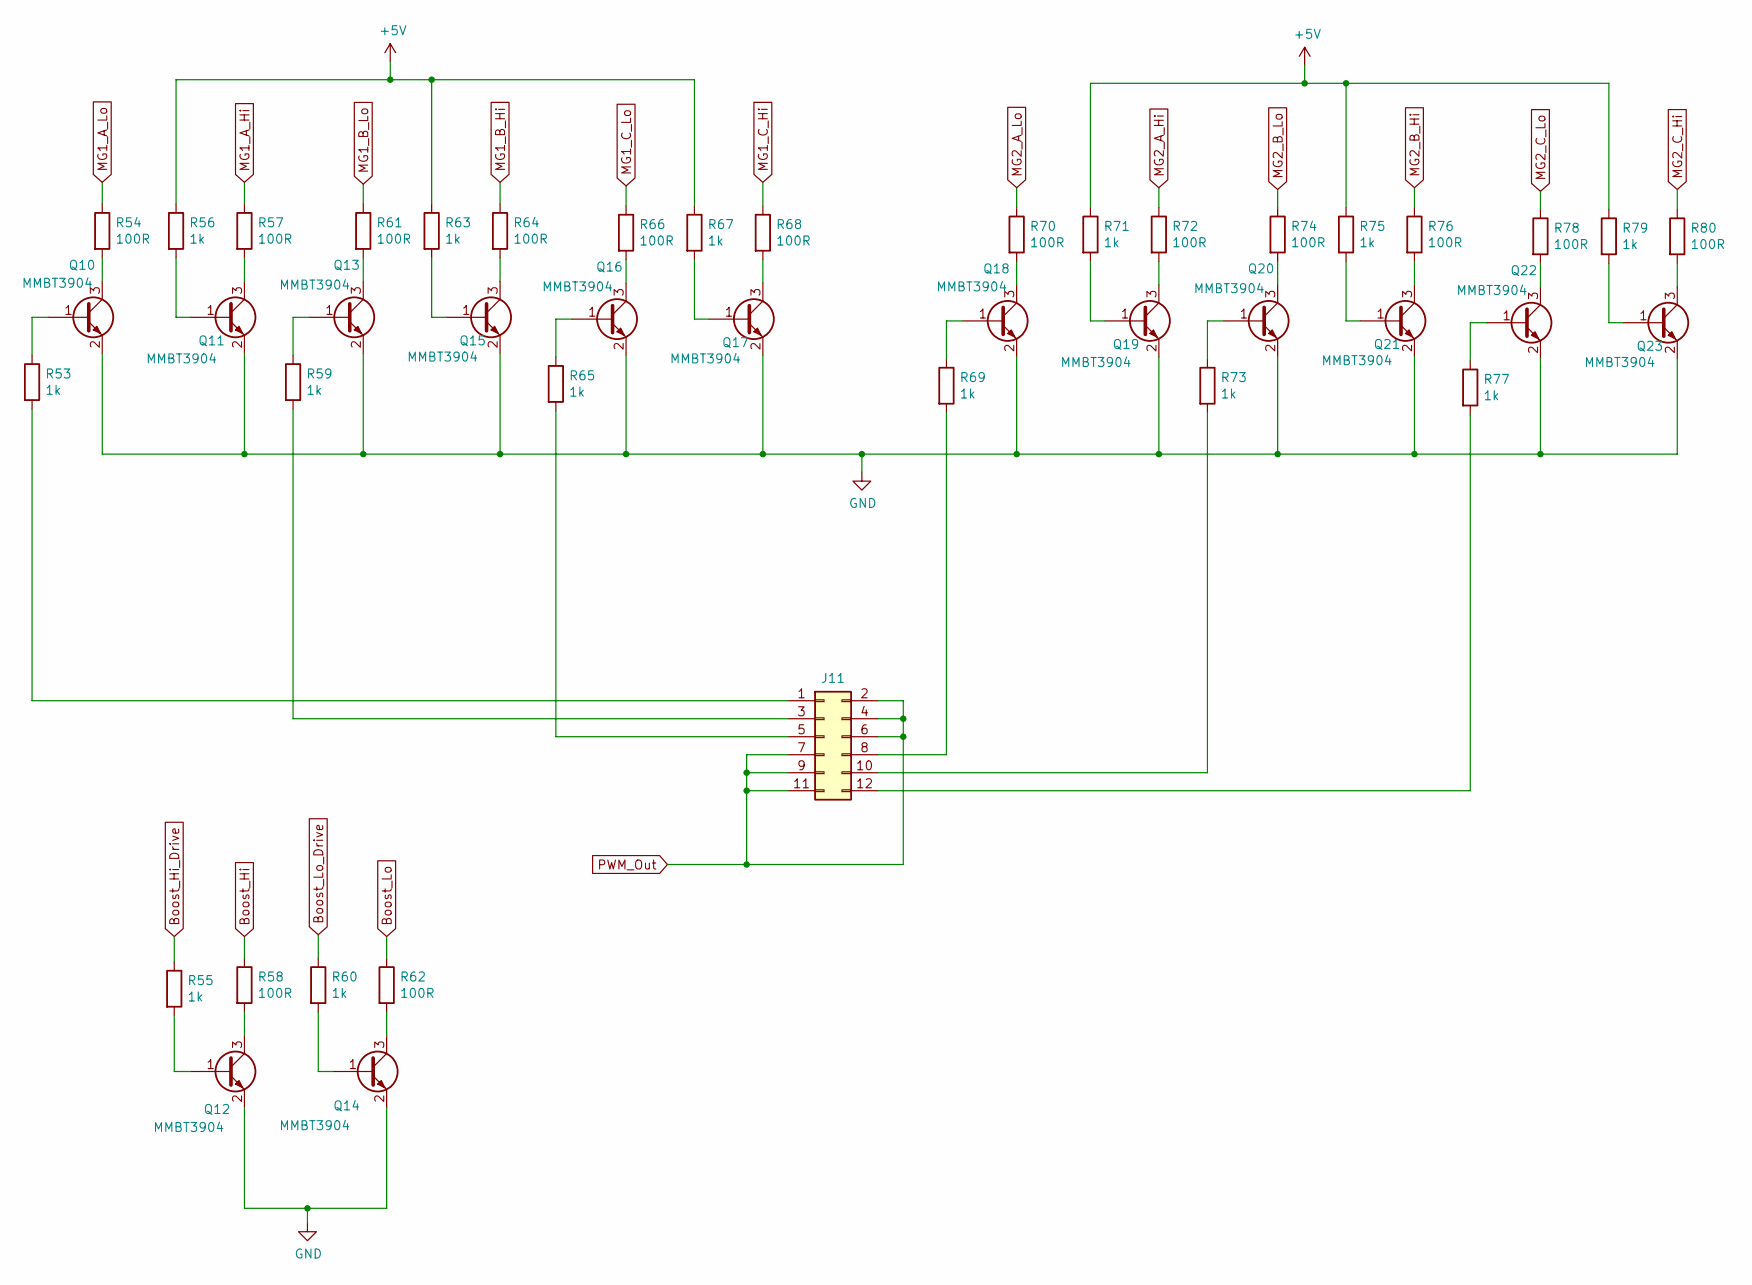
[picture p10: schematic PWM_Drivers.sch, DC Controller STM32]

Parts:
J11: Conn_02x06_Odd_Even; PinHeader_2x06_P2.54mm_Vertical
Q10, Q11, Q12, Q13, Q14, Q15, Q16, Q17, Q18, Q19, Q20, Q21, Q22, Q23: MMBT3904; SOT-23
R53, R55, R56, R59, R60, R63, R65, R67, R69, R71, R73, R75, R77, R79: 1k; R_0603_1608Metric
R54, R57, R58, R61, R62, R64, R66, R68, R70, R72, R74, R76, R78, R80: 100R; R_0603_1608Metric

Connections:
+5V: R56.1, R63.1, R67.1, R71.1, R75.1, R79.1; also elsewhere on the board
Boost_Hi: R58.1; also elsewhere on the board
Boost_Hi_Drive: R55.1; also elsewhere on the board
Boost_Lo: R62.1; also elsewhere on the board
Boost_Lo_Drive: R60.1; also elsewhere on the board
GND: Q10.2 (E), Q11.2 (E), Q12.2 (E), Q13.2 (E), Q14.2 (E), Q15.2 (E), Q16.2 (E), Q17.2 (E), Q18.2 (E), Q19.2 (E), Q20.2 (E), Q21.2 (E), Q22.2 (E), Q23.2 (E); also elsewhere on the board
MG1_A_Hi: R57.1; also elsewhere on the board
MG1_A_Lo: R54.1; also elsewhere on the board
MG1_B_Hi: R64.1; also elsewhere on the board
MG1_B_Lo: R61.1; also elsewhere on the board
MG1_C_Hi: R68.1; also elsewhere on the board
MG1_C_Lo: R66.1; also elsewhere on the board
MG2_A_Hi: R72.1; also elsewhere on the board
MG2_A_Lo: R70.1; also elsewhere on the board
MG2_B_Hi: R76.1; also elsewhere on the board
MG2_B_Lo: R74.1; also elsewhere on the board
MG2_C_Hi: R80.1; also elsewhere on the board
MG2_C_Lo: R78.1; also elsewhere on the board
unnamed: J11.1, R53.2
unnamed: J11.3, R59.2
unnamed: J11.5, R65.2
unnamed: J11.8, R69.2
unnamed: J11.10, R73.2
unnamed: J11.12, R77.2
unnamed: Q10.1 (B), R53.1
unnamed: Q10.3 (C), R54.2
unnamed: Q11.1 (B), R56.2
unnamed: Q11.3 (C), R57.2
unnamed: Q12.1 (B), R55.2
unnamed: Q12.3 (C), R58.2
unnamed: Q13.1 (B), R59.1
unnamed: Q13.3 (C), R61.2
unnamed: Q14.1 (B), R60.2
unnamed: Q14.3 (C), R62.2
unnamed: Q15.1 (B), R63.2
unnamed: Q15.3 (C), R64.2
unnamed: Q16.1 (B), R65.1
unnamed: Q16.3 (C), R66.2
unnamed: Q17.1 (B), R67.2
unnamed: Q17.3 (C), R68.2
unnamed: Q18.1 (B), R69.1
unnamed: Q18.3 (C), R70.2
unnamed: Q19.1 (B), R71.2
unnamed: Q19.3 (C), R72.2
unnamed: Q20.1 (B), R73.1
unnamed: Q20.3 (C), R74.2
unnamed: Q21.1 (B), R75.2
unnamed: Q21.3 (C), R76.2
unnamed: Q22.1 (B), R77.1
unnamed: Q22.3 (C), R78.2
unnamed: Q23.1 (B), R79.2
unnamed: Q23.3 (C), R80.2
PWM_Out: J11.2, J11.4, J11.6, J11.7, J11.9, J11.11; also elsewhere on the board

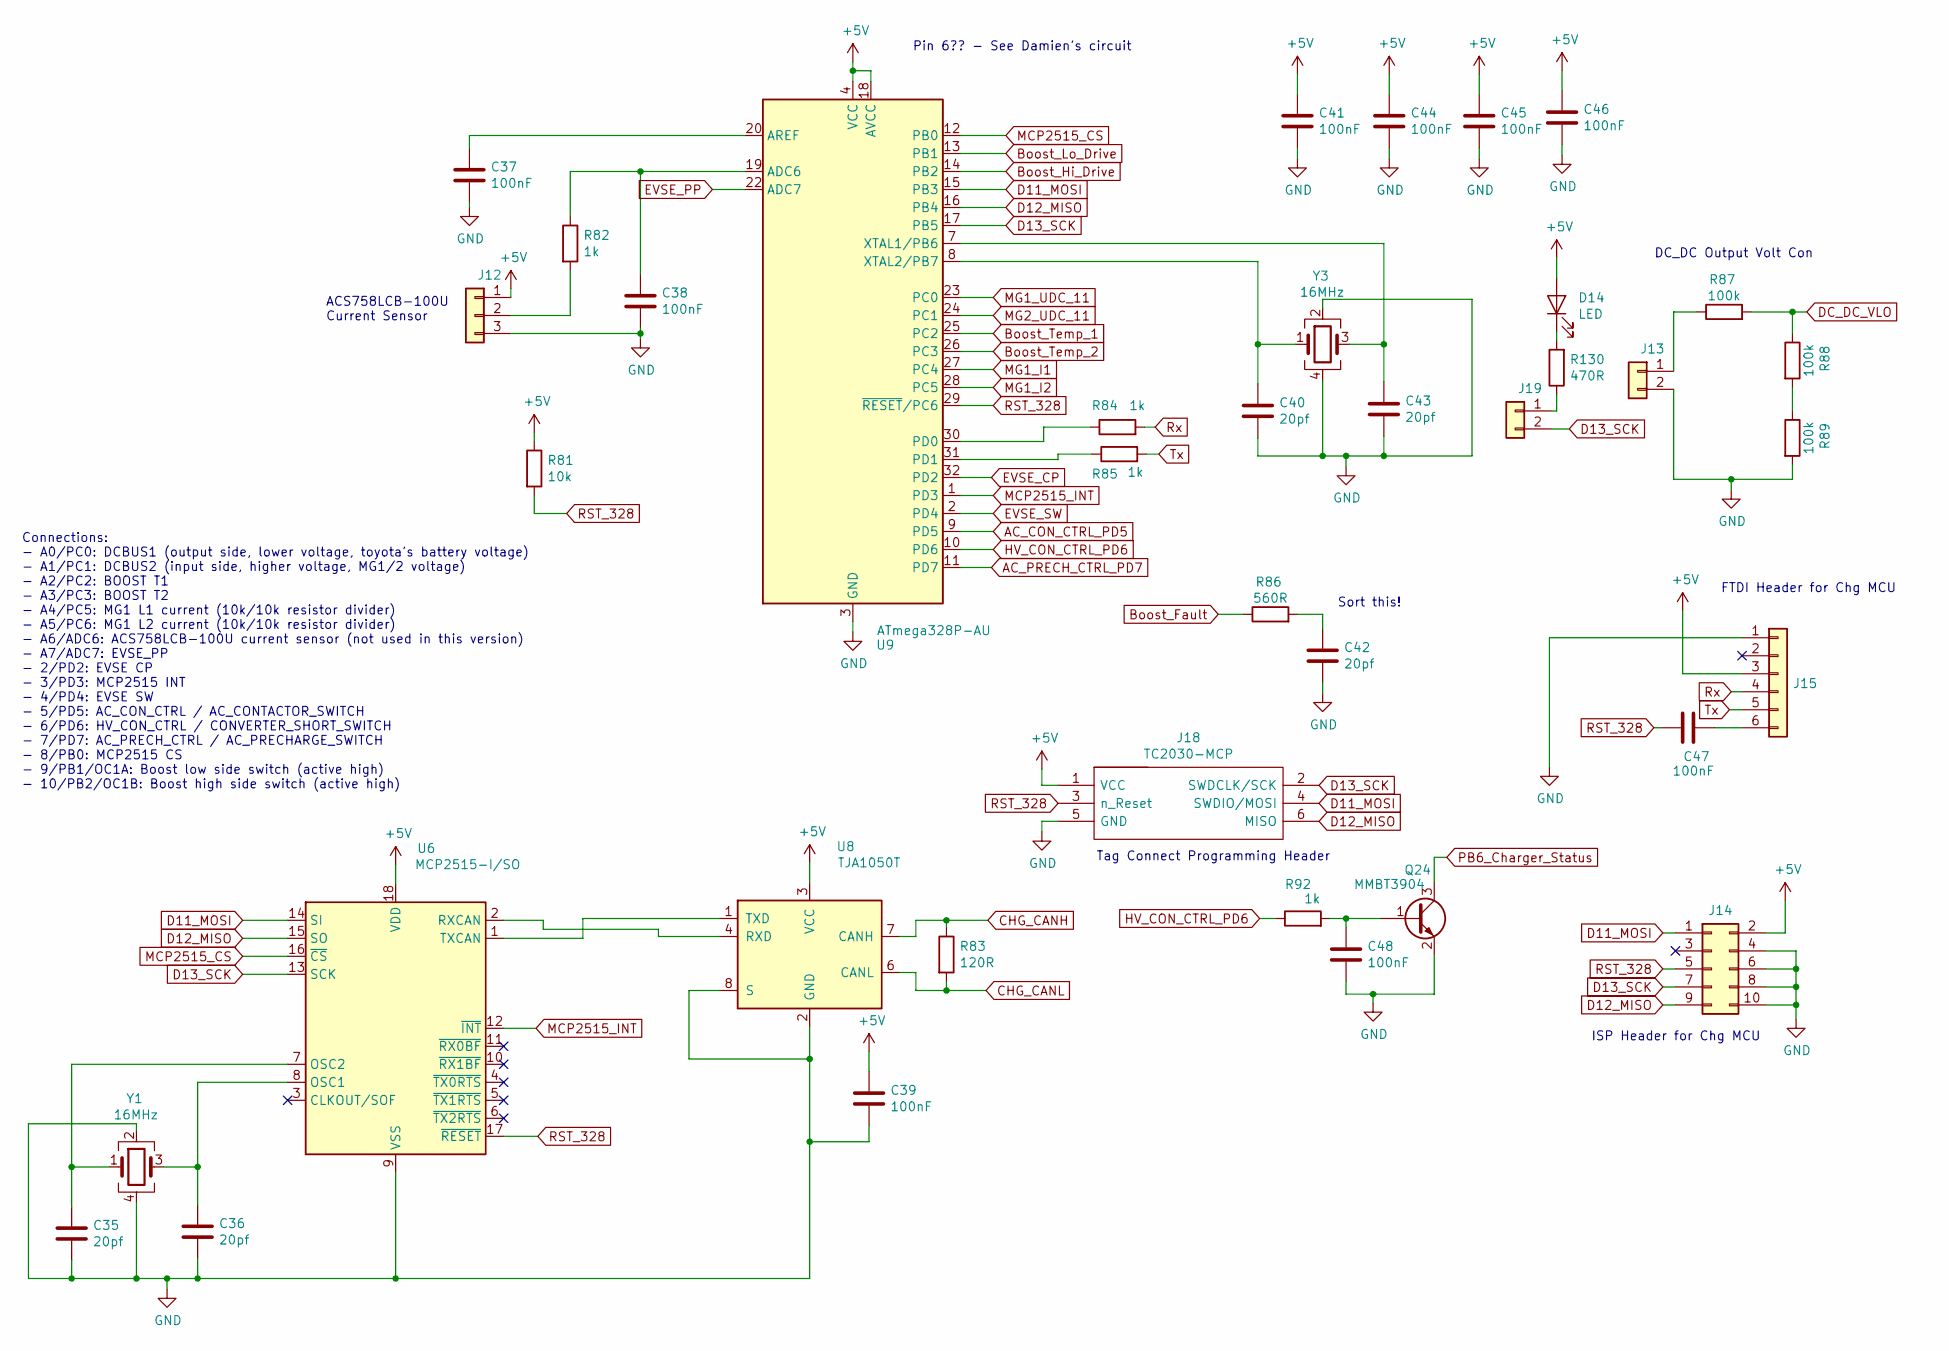
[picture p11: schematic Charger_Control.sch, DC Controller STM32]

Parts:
C35, C36, C40, C42, C43: 20pf; C_0603_1608Metric
C37, C38, C39, C41, C44, C45, C46, C47, C48: 100nF; C_0603_1608Metric
D14: LED; LED_0805_2012Metric
J12: Conn_01x03; PinHeader_1x03_P2.54mm_Vertical
J13, J19: Conn_01x02; PinHeader_1x02_P2.54mm_Vertical
J14: Conn_02x05_Odd_Even; PinHeader_2x05_P2.54mm_Vertical
J15: Conn_01x06; PinHeader_1x06_P2.54mm_Vertical
J18: TC2030-MCP; TC2030MCP; Manufacturer_Part_Number TC2030-MCP
Q24: MMBT3904; SOT-23
R81: 10k; R_0603_1608Metric
R82, R84, R85, R92: 1k; R_0603_1608Metric
R83: 120R; R_0603_1608Metric
R86: 560R; R_0603_1608Metric
R87, R88, R89: 100k; R_0603_1608Metric
R130: 470R; R_0603_1608Metric
U6: MCP2515-I/SO; SOIC-18W_7.5x11.6mm_P1.27mm
U8: TJA1050T; SOIC-8_3.9x4.9mm_P1.27mm
U9: ATmega328P-AU; TQFP-32_7x7mm_P0.8mm
Y1, Y3: 16MHz; Crystal_SMD_3225-4Pin_3.2x2.5mm

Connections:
+5V: C39.1, C41.1, C44.1, C45.1, C46.1, D14.2 (A), J12.1, J14.2, J15.3, J18.1 (VCC), R81.1, U6.18 (VDD), U8.3 (VCC), U9.4 (VCC), U9.6 (VCC), U9.18 (AVCC); also elsewhere on the board
AC_CON_CTRL_PD5: U9.9 (PD5); also elsewhere on the board
AC_PRECH_CTRL_PD7: U9.11 (PD7); also elsewhere on the board
Boost_Fault: R86.1; also elsewhere on the board
Boost_Hi_Drive: U9.14 (PB2); also elsewhere on the board
Boost_Lo_Drive: U9.13 (PB1); also elsewhere on the board
Boost_Temp_1: U9.25 (PC2); also elsewhere on the board
Boost_Temp_2: U9.26 (PC3); also elsewhere on the board
CHG_CANH: R83.1, U8.7 (CANH); also elsewhere on the board
CHG_CANL: R83.2, U8.6 (CANL); also elsewhere on the board
D11_MOSI: J14.1, J18.4 (SWDIO/MOSI), U6.14 (SI), U9.15 (PB3)
D12_MISO: J14.9, J18.6 (MISO), U6.15 (SO), U9.16 (PB4)
D13_SCK: J14.7, J18.2 (SWDCLK/SCK), J19.2, U6.13 (SCK), U9.17 (PB5)
DC_DC_VLO: R87.2, R88.1; also elsewhere on the board
EVSE_CP: U9.32 (PD2); also elsewhere on the board
EVSE_PP: U9.22 (ADC7); also elsewhere on the board
EVSE_SW: U9.2 (PD4); also elsewhere on the board
GND: C35.2, C36.2, C37.2, C38.2, C39.2, C40.2, C41.2, C42.2, C43.2, C44.2, C45.2, C46.2, C48.2, J12.3, J13.2, J14.4, J14.6, J14.8, J14.10, J15.1, J18.5 (GND), Q24.2 (E), R89.2, U6.9 (VSS), U8.2 (GND), U8.8 (S), U9.3 (GND), U9.5 (GND), U9.21 (GND), Y1.2, Y1.4, Y3.2, Y3.4; also elsewhere on the board
HV_CON_CTRL_PD6: R92.1, U9.10 (PD6); also elsewhere on the board
MCP2515_CS: U6.16 (~CS), U9.12 (PB0)
MCP2515_INT: U6.12 (~INT), U9.1 (PD3)
MG1_I1: U9.27 (PC4); also elsewhere on the board
MG1_I2: U9.28 (PC5); also elsewhere on the board
MG1_UDC_11: U9.23 (PC0); also elsewhere on the board
MG2_UDC_11: U9.24 (PC1); also elsewhere on the board
unnamed: C35.1, U6.7 (OSC2), Y1.1
unnamed: C36.1, U6.8 (OSC1), Y1.3
unnamed: C37.1, U9.20 (AREF)
unnamed: C38.1, R82.1, U9.19 (ADC6)
unnamed: C40.1, U9.8 (XTAL2/PB7), Y3.1
unnamed: C42.1, R86.2
unnamed: C43.1, U9.7 (XTAL1/PB6), Y3.3
unnamed: C47.1, J15.6
unnamed: C48.1, Q24.1 (B), R92.2
unnamed: D14.1 (K), R130.2
unnamed: J12.2, R82.2
unnamed: J13.1, R87.1
unnamed: J19.1, R130.1
unnamed: R84.1, U9.30 (PD0)
unnamed: R85.1, U9.31 (PD1)
unnamed: R88.2, R89.1
unnamed: U6.1 (TXCAN), U8.1 (TXD)
unnamed: U6.2 (RXCAN), U8.4 (RXD)
PB6_Charger_Status: Q24.3 (C); also elsewhere on the board
RST_328: C47.2, J14.5, J18.3 (n_Reset), R81.2, U6.17 (~RESET), U9.29 (~RESET~/PC6)
Rx: J15.4, R84.2
Tx: J15.5, R85.2

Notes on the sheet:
Pin 6?? - See Damien's circuit
ACS758LCB-100U Current Sensor
Sort this!
DC_DC Output Volt Con
FTDI Header for Chg MCU
ISP Header for Chg MCU
Connections: - A0/PC0: DCBUS1 (output side, lower voltage, toyota's battery voltage) - A1/PC1: DCBUS2 (input side, higher voltage, MG1/2 voltage) - A2/PC2: BOOST T1 - A3/PC3: BOOST T2 - A4/PC5: MG1 L1 current (10k/10k resistor divider) - A5/PC6: MG1 L2 current (10k/10k resistor divider) - A6/ADC6: 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
Tag Connect Programming Header

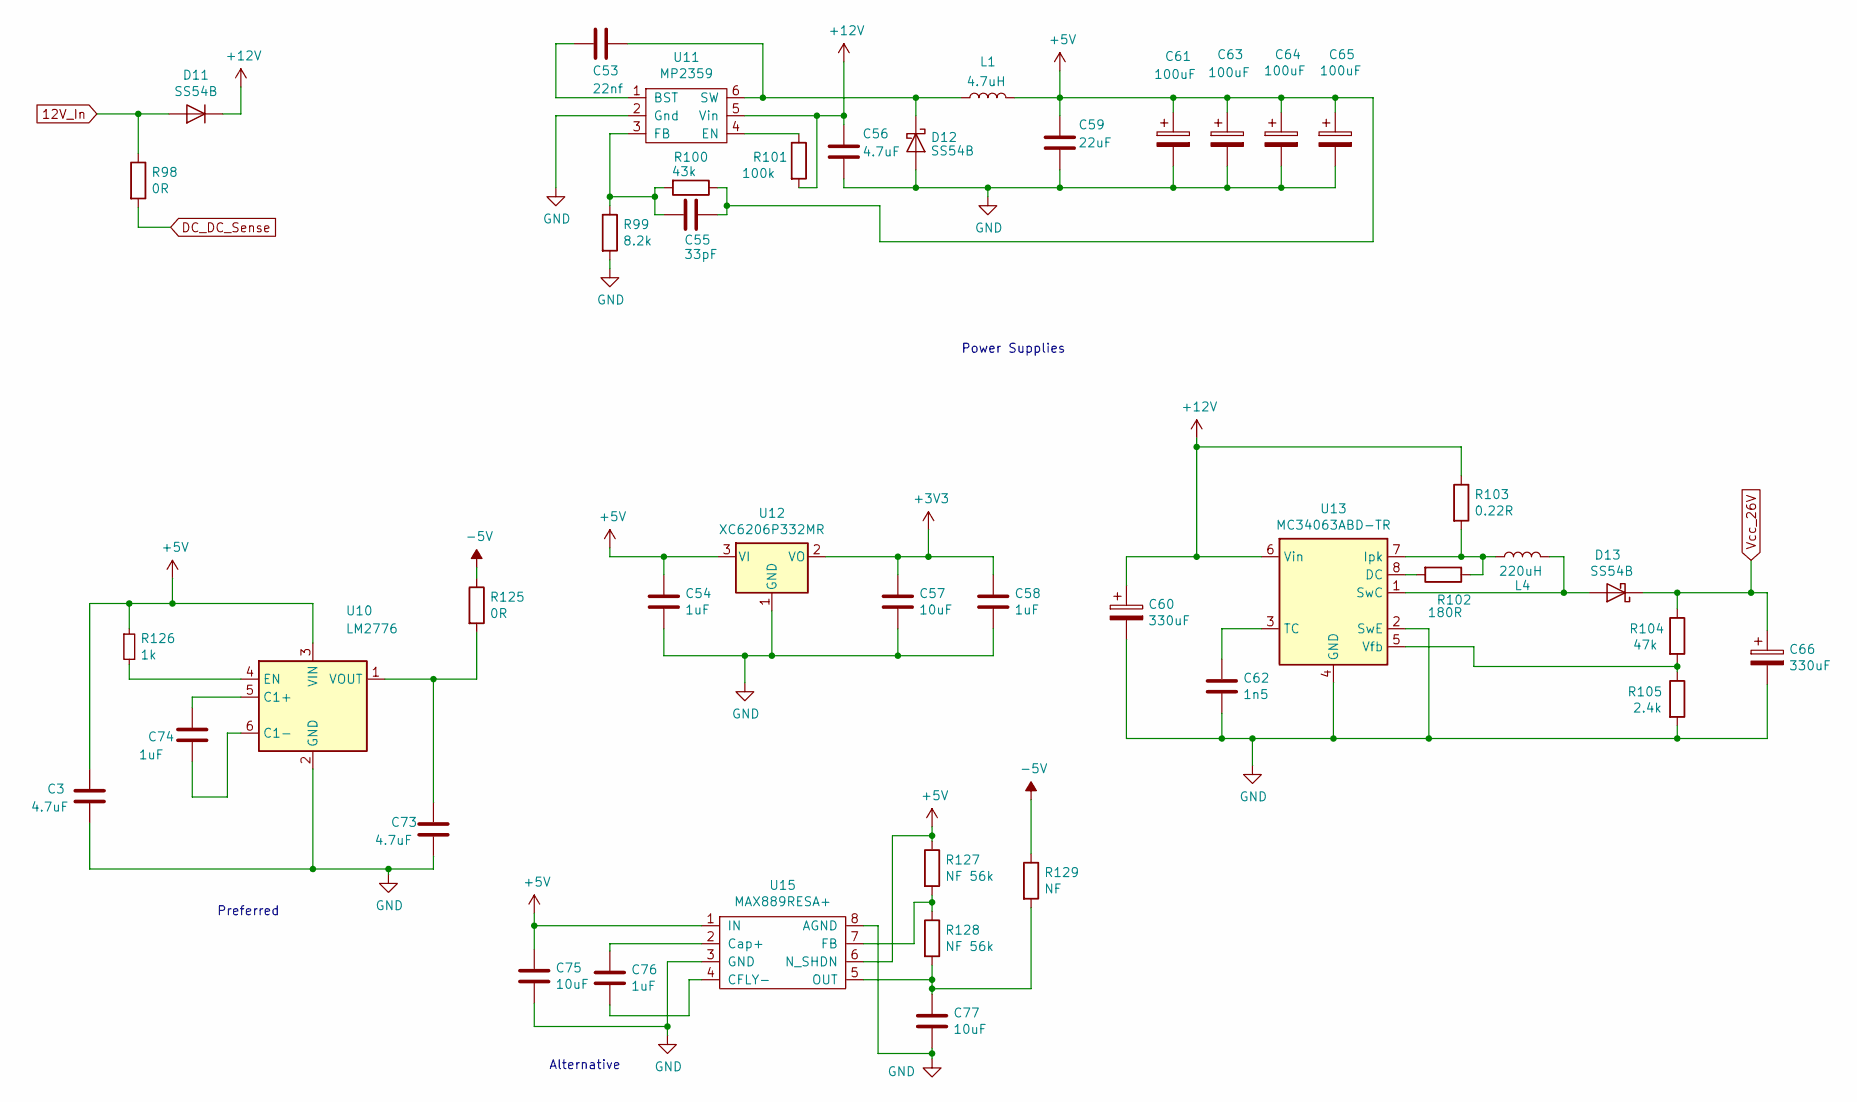
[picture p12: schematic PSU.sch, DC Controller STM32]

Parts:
C3, C56, C73: 4.7uF; C_0805_2012Metric
C53: 22nf; C_0603_1608Metric
C54, C58, C76: 1uF; C_0603_1608Metric
C55: 33pF; C_0603_1608Metric
C57, C75, C77: 10uF; C_0805_2012Metric
C59: 22uF; C_0805_2012Metric
C60, C66: 330uF; CP_Elec_10x10
C61, C63, C64, C65: 100uF; CP_EIA-3528-21_Kemet-B
C62: 1n5; C_0805_2012Metric
C74: 1uF; C_0805_2012Metric
D11, D12, D13: SS54B; D_SMA
L1: 4.7uH; L_1210_3225Metric
L4: 220uH; L_12x12mm_H6mm
R98, R125: 0R; R_0603_1608Metric
R99: 8.2k; R_0603_1608Metric
R100: 43k; R_0603_1608Metric
R101: 100k; R_0603_1608Metric
R102: 180R; R_0603_1608Metric
R103: 0.22R; R_0805_2012Metric
R104: 47k; R_0603_1608Metric
R105: 2.4k; R_0603_1608Metric
R126: 1k; R_0603_1608Metric
R127, R128: NF 56k; R_0603_1608Metric
R129: NF; R_0603_1608Metric
U10: LM2776; SOT-23-6
U11: MP2359; TSOT-23-6
U12: XC6206P332MR; SOT-23
U13: MC34063ABD-TR; SOIC-8_3.9x4.9mm_P1.27mm
U15: MAX889RESA+; SOIC-8_3.9x4.9mm_P1.27mm

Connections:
12V_In: D11.2 (A), R98.1; also elsewhere on the board
+3V3: C57.1, C58.1, U12.2 (VO); also elsewhere on the board
+5V: C3.1, C54.1, C55.1, C59.1, C61.1, C63.1, C64.1, C65.1, C75.1, L1.2, R100.1, R126.1, R127.1, U10.3 (VIN), U12.3 (VI), U15.1 (IN), U15.6 (N_SHDN); also elsewhere on the board
+12V: C56.1, C60.1, D11.1 (K), R101.2, R103.1, U11.5 (Vin), U13.6 (Vin); also elsewhere on the board
-5V: R125.1, R129.1; also elsewhere on the board
DC_DC_Sense: R98.2; also elsewhere on the board
GND: C3.2, C54.2, C56.2, C57.2, C58.2, C59.2, C60.2, C61.2, C62.2, C63.2, C64.2, C65.2, C66.2, C73.2, C75.2, C77.2, D12.2 (A), R99.2, R105.2, U10.2 (GND), U11.2 (Gnd), U12.1 (GND), U13.2 (SwE), U13.4 (GND), U15.3 (GND), U15.8 (AGND); also elsewhere on the board
unnamed: C53.1, D12.1 (K), L1.1, U11.6 (SW)
unnamed: C53.2, U11.1 (BST)
unnamed: C55.2, R99.1, R100.2, U11.3 (FB)
unnamed: C62.1, U13.3 (TC)
unnamed: C73.1, R125.2, U10.1 (VOUT)
unnamed: C74.1, U10.5 (C1+)
unnamed: C74.2, U10.6 (C1-)
unnamed: C76.1, U15.2 (Cap+)
unnamed: C76.2, U15.4 (CFLY-)
unnamed: C77.1, R128.2, R129.2, U15.5 (OUT)
unnamed: D13.2 (A), L4.2, U13.1 (SwC)
unnamed: L4.1, R102.1, R103.2, U13.7 (Ipk)
unnamed: R101.1, U11.4 (EN)
unnamed: R102.2, U13.8 (DC)
unnamed: R104.2, R105.1, U13.5 (Vfb)
unnamed: R126.2, U10.4 (EN)
unnamed: R127.2, R128.1, U15.7 (FB)
Vcc_26V: C66.1, D13.1 (K), R104.1; also elsewhere on the board

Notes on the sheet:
Power Supplies
Preferred
Alternative

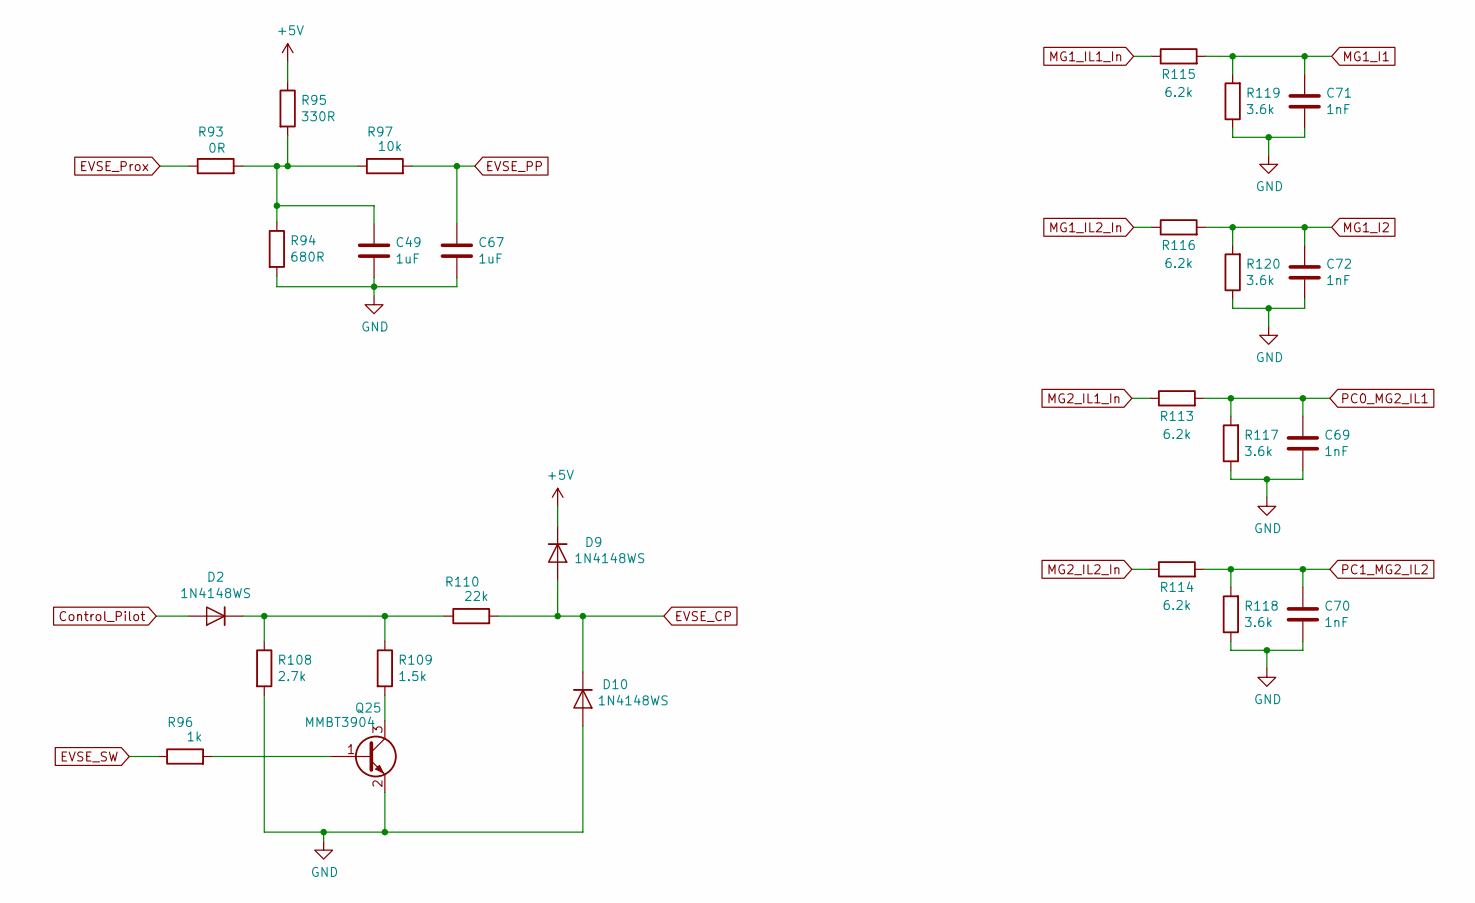
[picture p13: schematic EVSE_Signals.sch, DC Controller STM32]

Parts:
C49, C67: 1uF; C_0603_1608Metric
C69, C70, C71, C72: 1nF; C_0603_1608Metric
D2, D9, D10: 1N4148WS; D_SOD-323
Q25: MMBT3904; SOT-23
R93: 0R; R_0603_1608Metric
R94: 680R; R_0603_1608Metric
R95: 330R; R_0603_1608Metric
R96: 1k; R_0603_1608Metric
R97: 10k; R_0603_1608Metric
R108: 2.7k; R_0603_1608Metric
R109: 1.5k; R_0603_1608Metric
R110: 22k; R_0603_1608Metric
R113, R114, R115, R116: 6.2k; R_0603_1608Metric
R117, R118, R119, R120: 3.6k; R_0603_1608Metric

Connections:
+5V: D9.1 (K), R95.1; also elsewhere on the board
Control_Pilot: D2.2 (A); also elsewhere on the board
EVSE_CP: D9.2 (A), D10.1 (K), R110.2; also elsewhere on the board
EVSE_PP: C67.1, R97.2; also elsewhere on the board
EVSE_Prox: R93.1; also elsewhere on the board
EVSE_SW: R96.1; also elsewhere on the board
GND: C49.2, C67.2, C69.2, C70.2, C71.2, C72.2, D10.2 (A), Q25.2 (E), R94.2, R108.2, R117.1, R118.1, R119.1, R120.1; also elsewhere on the board
MG1_I1: C71.1, R115.2, R119.2; also elsewhere on the board
MG1_I2: C72.1, R116.2, R120.2; also elsewhere on the board
MG1_IL1_In: R115.1; also elsewhere on the board
MG1_IL2_In: R116.1; also elsewhere on the board
MG2_IL1_In: R113.1; also elsewhere on the board
MG2_IL2_In: R114.1; also elsewhere on the board
unnamed: C49.1, R93.2, R94.1, R95.2, R97.1
unnamed: D2.1 (K), R108.1, R109.1, R110.1
unnamed: Q25.1 (B), R96.2
unnamed: Q25.3 (C), R109.2
PC0_MG2_IL1: C69.1, R113.2, R117.2; also elsewhere on the board
PC1_MG2_IL2: C70.1, R114.2, R118.2; also elsewhere on the board

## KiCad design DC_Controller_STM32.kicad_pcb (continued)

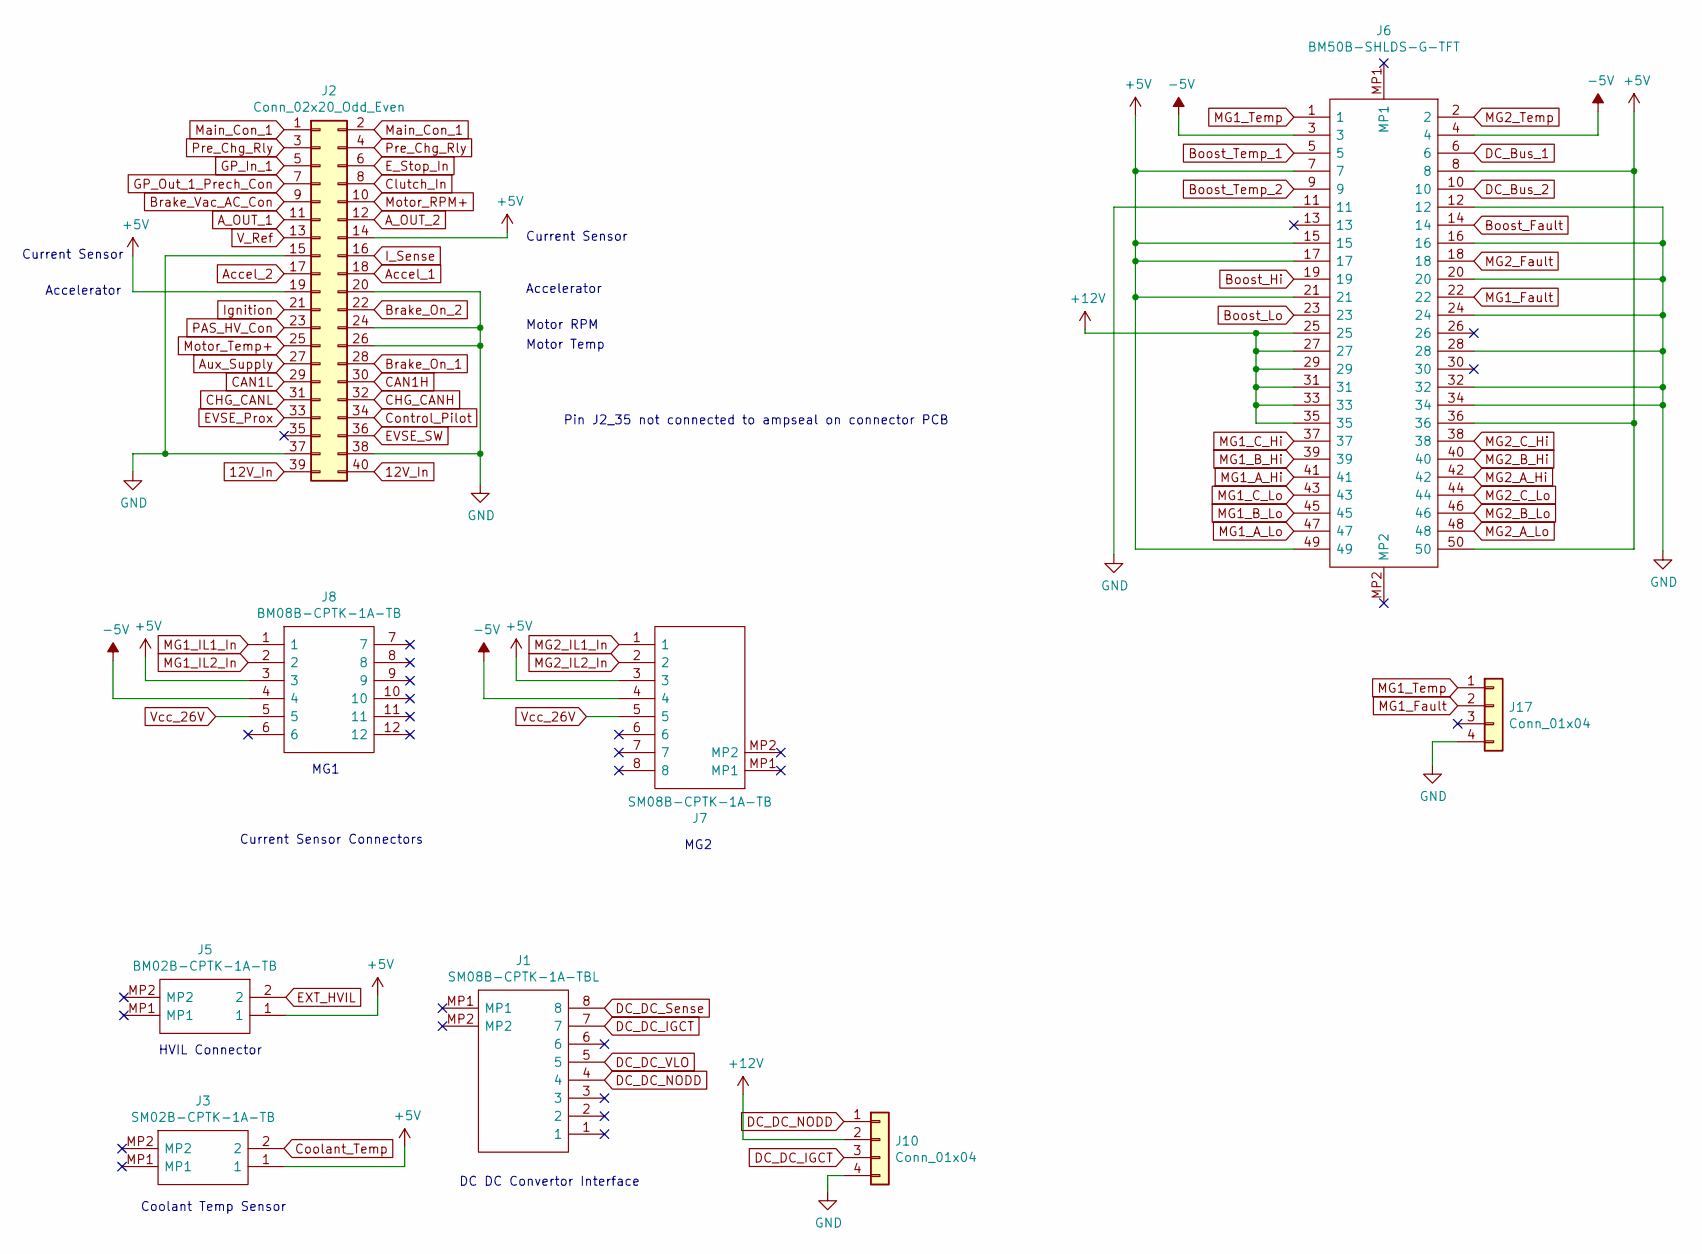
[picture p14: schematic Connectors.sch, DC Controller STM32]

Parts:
J1: SM08B-CPTK-1A-TBL; SM08BCPTK1ATBL; Mouser Part Number 306-SM08B-CPTK-1ATBL
J2: Conn_02x20_Odd_Even; IDC-Header_2x20_P2.54mm_Horizontal
J3: SM02B-CPTK-1A-TB; SM02BCPTK1ATB; Mouser Part Number 306-SM02B-CPTK-1A-TB
J5: BM02B-CPTK-1A-TB; BM02BCPTK1ATB; Mouser Part Number 306-BM02B-CPTK-1A-TB
J6: BM50B-SHLDS-G-TFT; BM50BSHLDSGTFT; Manufacturer_Part_Number BM50B-SHLDS-G-TFT
J7: SM08B-CPTK-1A-TB; SM08BCPTK1ATBL_odd_even; Manufacturer_Part_Number SM08B-CPTK-1A-TB
J8: BM08B-CPTK-1A-TB; BM08BCPTK1ATB; Mouser Part Number 306-BM08B-CPTK-1A-TB
J10, J17: Conn_01x04; PinHeader_1x04_P2.54mm_Vertical

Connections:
12V_In: J2.39, J2.40; also elsewhere on the board
+5V: J2.14, J2.19, J3.1, J5.1, J6.7, J6.8, J6.15, J6.17, J6.21, J6.36, J6.49, J6.50, J7.3, J8.3; also elsewhere on the board
+12V: J6.25, J6.27, J6.29, J6.31, J6.33, J6.35, J10.2; also elsewhere on the board
-5V: J6.3, J6.4, J7.4, J8.4; also elsewhere on the board
A_OUT_1: J2.11; also elsewhere on the board
A_OUT_2: J2.12; also elsewhere on the board
Accel_1: J2.18; also elsewhere on the board
Accel_2: J2.17; also elsewhere on the board
Aux_Supply: J2.27; also elsewhere on the board
Boost_Fault: J6.14; also elsewhere on the board
Boost_Hi: J6.19; also elsewhere on the board
Boost_Lo: J6.23; also elsewhere on the board
Boost_Temp_1: J6.5; also elsewhere on the board
Boost_Temp_2: J6.9; also elsewhere on the board
Brake_On_1: J2.28; also elsewhere on the board
Brake_On_2: J2.22; also elsewhere on the board
Brake_Vac_AC_Con: J2.9; also elsewhere on the board
CAN1H: J2.30; also elsewhere on the board
CAN1L: J2.29; also elsewhere on the board
CHG_CANH: J2.32; also elsewhere on the board
CHG_CANL: J2.31; also elsewhere on the board
Clutch_In: J2.8; also elsewhere on the board
Control_Pilot: J2.34; also elsewhere on the board
Coolant_Temp: J3.2; also elsewhere on the board
DC_Bus_1: J6.6; also elsewhere on the board
DC_Bus_2: J6.10; also elsewhere on the board
DC_DC_IGCT: J1.7, J10.3
DC_DC_NODD: J1.4, J10.1
DC_DC_Sense: J1.8; also elsewhere on the board
DC_DC_VLO: J1.5; also elsewhere on the board
EVSE_Prox: J2.33; also elsewhere on the board
EVSE_SW: J2.36; also elsewhere on the board
EXT_HVIL: J5.2
E_Stop_In: J2.6; also elsewhere on the board
GND: J2.15, J2.20, J2.24, J2.26, J2.37, J2.38, J6.11, J6.12, J6.16, J6.20, J6.24, J6.28, J6.32, J6.34, J10.4, J17.4; also elsewhere on the board
GP_In_1: J2.5; also elsewhere on the board
GP_Out_1_Prech_Con: J2.7; also elsewhere on the board
I_Sense: J2.16; also elsewhere on the board
Ignition: J2.21; also elsewhere on the board
MG1_A_Hi: J6.41; also elsewhere on the board
MG1_A_Lo: J6.47; also elsewhere on the board
MG1_B_Hi: J6.39; also elsewhere on the board
MG1_B_Lo: J6.45; also elsewhere on the board
MG1_C_Hi: J6.37; also elsewhere on the board
MG1_C_Lo: J6.43; also elsewhere on the board
MG1_Fault: J6.22, J17.2
MG1_IL1_In: J8.1; also elsewhere on the board
MG1_IL2_In: J8.2; also elsewhere on the board
MG1_Temp: J6.1, J17.1
MG2_A_Hi: J6.42; also elsewhere on the board
MG2_A_Lo: J6.48; also elsewhere on the board
MG2_B_Hi: J6.40; also elsewhere on the board
MG2_B_Lo: J6.46; also elsewhere on the board
MG2_C_Hi: J6.38; also elsewhere on the board
MG2_C_Lo: J6.44; also elsewhere on the board
MG2_Fault: J6.18; also elsewhere on the board
MG2_IL1_In: J7.1; also elsewhere on the board
MG2_IL2_In: J7.2; also elsewhere on the board
MG2_Temp: J6.2; also elsewhere on the board
Main_Con_1: J2.1, J2.2; also elsewhere on the board
Motor_RPM+: J2.10; also elsewhere on the board
Motor_Temp+: J2.25; also elsewhere on the board
PAS_HV_Con: J2.23; also elsewhere on the board
Pre_Chg_Rly: J2.3, J2.4; also elsewhere on the board
V_Ref: J2.13; also elsewhere on the board
Vcc_26V: J7.5, J8.5; also elsewhere on the board

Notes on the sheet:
Current Sensor
Accelerator
Motor RPM
Motor Temp
DC DC Convertor Interface
HVIL Connector
Coolant Temp Sensor
Current Sensor Connectors
MG1
MG2
Pin J2_35 not connected to ampseal on connector PCB

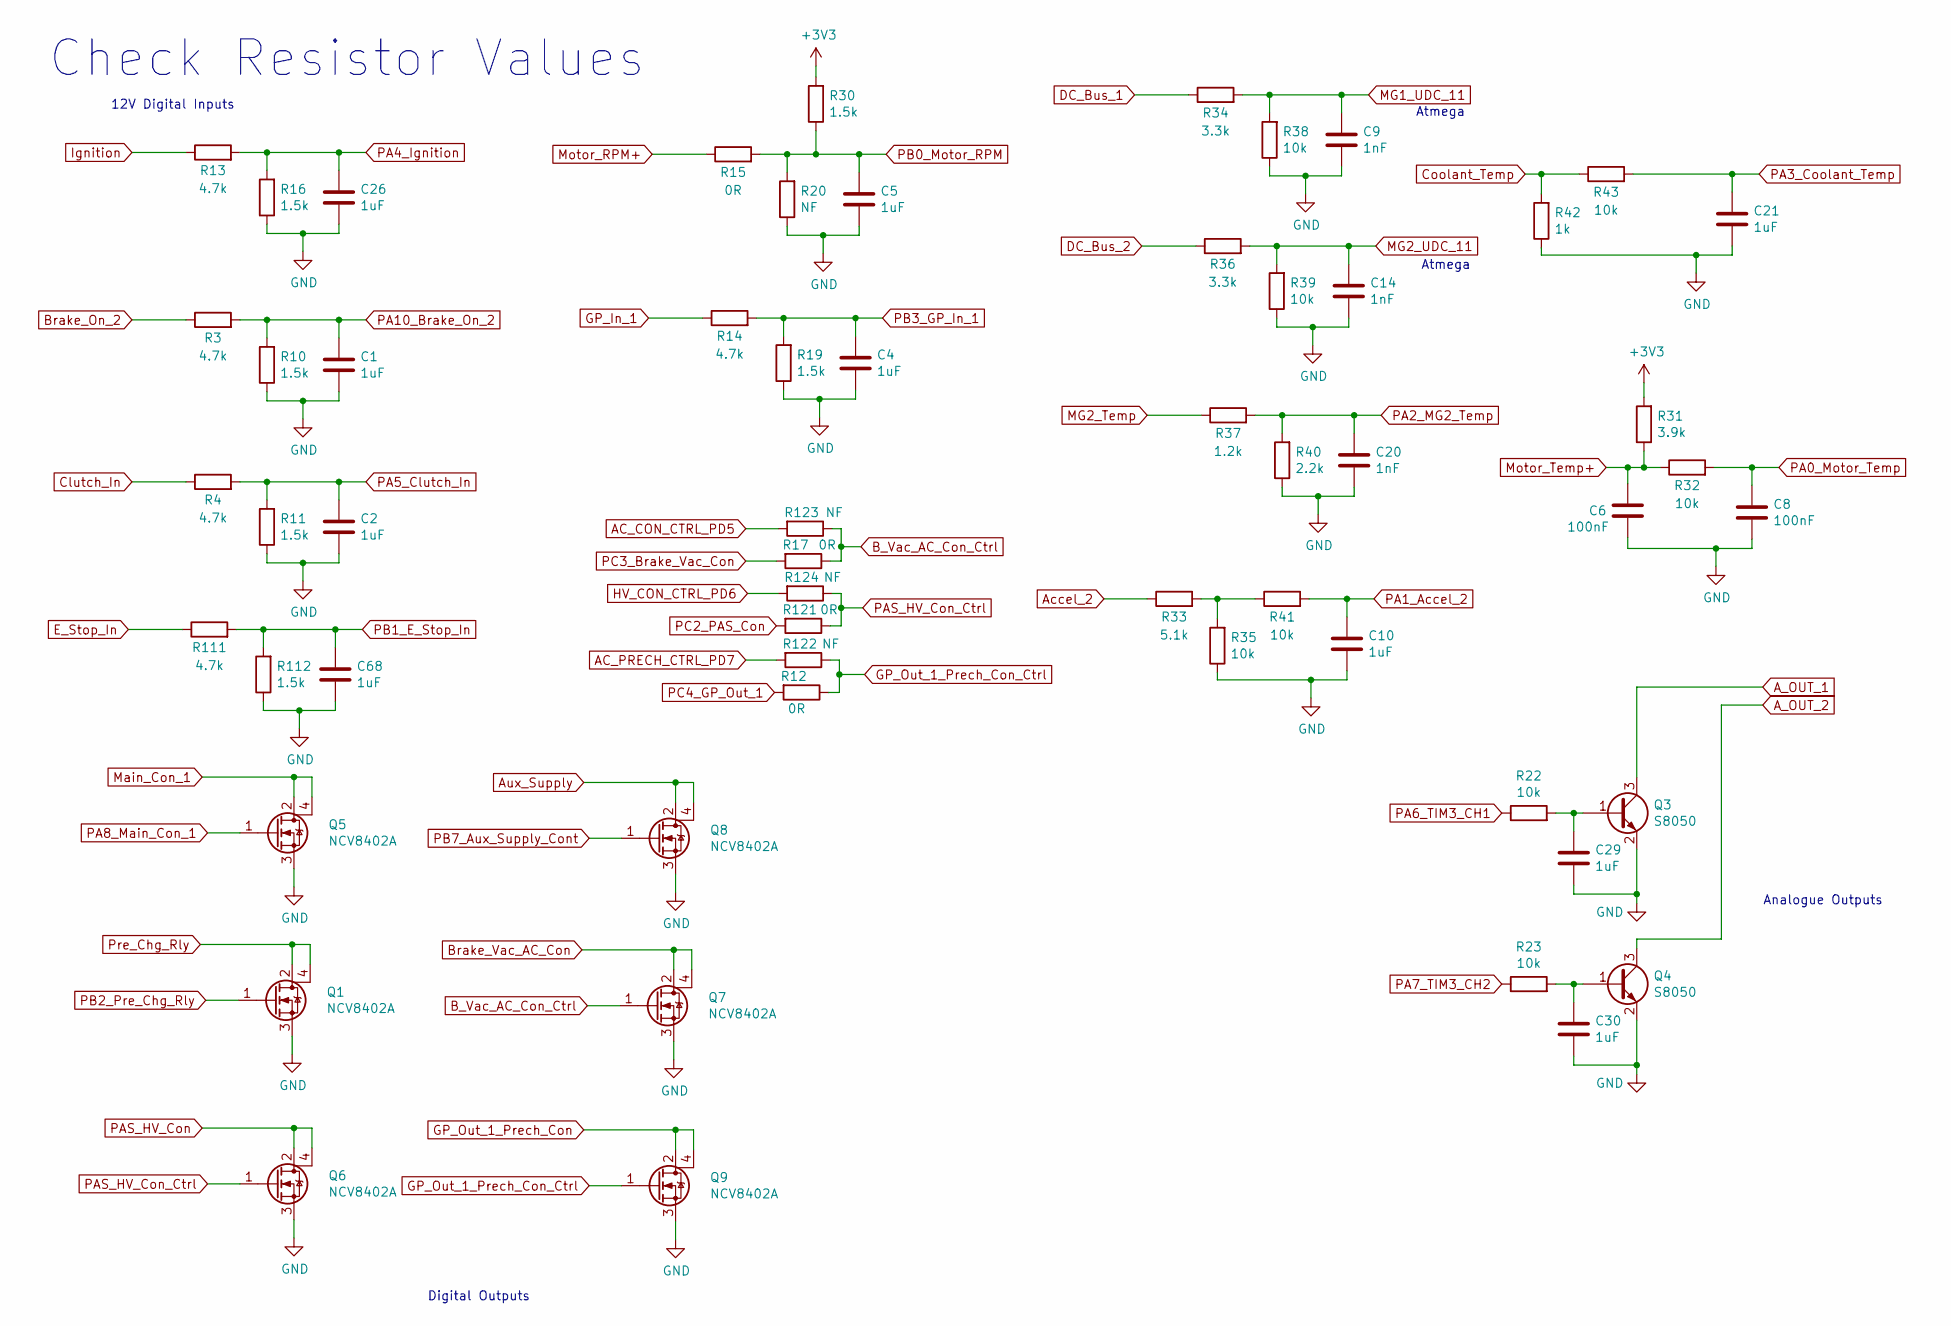
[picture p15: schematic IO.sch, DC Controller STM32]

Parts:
C1, C2, C4, C5, C10, C21, C26, C29, C30, C68: 1uF; C_0603_1608Metric
C6, C8: 100nF; C_0603_1608Metric
C9, C14, C20: 1nF; C_0603_1608Metric
Q1, Q5, Q6, Q7, Q8, Q9: NCV8402A; SOT-223
Q3, Q4: S8050; SOT-23
R3, R4, R13, R14, R111: 4.7k; R_0603_1608Metric
R10, R11, R16, R19, R30, R112: 1.5k; R_0603_1608Metric
R12, R15, R17, R121: 0R; R_0603_1608Metric
R20, R122, R123, R124: NF; R_0603_1608Metric
R22, R23, R32, R35, R38, R39, R41, R43: 10k; R_0603_1608Metric
R31: 3.9k; R_0603_1608Metric
R33: 5.1k; R_0603_1608Metric
R34, R36: 3.3k; R_0603_1608Metric
R37: 1.2k; R_0603_1608Metric
R40: 2.2k; R_0603_1608Metric
R42: 1k; R_0603_1608Metric

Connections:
+3V3: R30.2, R31.2; also elsewhere on the board
AC_CON_CTRL_PD5: R123.2; also elsewhere on the board
AC_PRECH_CTRL_PD7: R122.2; also elsewhere on the board
A_OUT_1: Q3.3 (C); also elsewhere on the board
A_OUT_2: Q4.3 (C); also elsewhere on the board
Accel_2: R33.1; also elsewhere on the board
Aux_Supply: Q8.2 (D), Q8.4 (D); also elsewhere on the board
B_Vac_AC_Con_Ctrl: Q7.1 (G), R17.1, R123.1
Brake_On_2: R3.1; also elsewhere on the board
Brake_Vac_AC_Con: Q7.2 (D), Q7.4 (D); also elsewhere on the board
Clutch_In: R4.1; also elsewhere on the board
Coolant_Temp: R42.2, R43.1; also elsewhere on the board
DC_Bus_1: R34.1; also elsewhere on the board
DC_Bus_2: R36.1; also elsewhere on the board
E_Stop_In: R111.1; also elsewhere on the board
GND: C1.2, C2.2, C4.2, C5.2, C6.2, C8.2, C9.2, C10.2, C14.2, C20.2, C21.2, C26.2, C29.2, C30.2, C68.2, Q1.3 (S), Q3.2 (E), Q4.2 (E), Q5.3 (S), Q6.3 (S), Q7.3 (S), Q8.3 (S), Q9.3 (S), R10.1, R11.1, R16.1, R19.1, R20.1, R35.1, R38.1, R39.1, R40.1, R42.1, R112.1; also elsewhere on the board
GP_In_1: R14.1; also elsewhere on the board
GP_Out_1_Prech_Con: Q9.2 (D), Q9.4 (D); also elsewhere on the board
GP_Out_1_Prech_Con_Ctrl: Q9.1 (G), R12.1, R122.1
HV_CON_CTRL_PD6: R124.2; also elsewhere on the board
Ignition: R13.1; also elsewhere on the board
MG1_UDC_11: C9.1, R34.2, R38.2; also elsewhere on the board
MG2_Temp: R37.1; also elsewhere on the board
MG2_UDC_11: C14.1, R36.2, R39.2; also elsewhere on the board
Main_Con_1: Q5.2 (D), Q5.4 (D); also elsewhere on the board
Motor_RPM+: R15.1; also elsewhere on the board
Motor_Temp+: C6.1, R31.1, R32.1; also elsewhere on the board
unnamed: C29.1, Q3.1 (B), R22.2
unnamed: C30.1, Q4.1 (B), R23.2
unnamed: R33.2, R35.2, R41.1
PA0_Motor_Temp: C8.1, R32.2; also elsewhere on the board
PA1_Accel_2: C10.1, R41.2; also elsewhere on the board
PA2_MG2_Temp: C20.1, R37.2, R40.2; also elsewhere on the board
PA3_Coolant_Temp: C21.1, R43.2; also elsewhere on the board
PA4_Ignition: C26.1, R13.2, R16.2; also elsewhere on the board
PA5_Clutch_In: C2.1, R4.2, R11.2; also elsewhere on the board
PA6_TIM3_CH1: R22.1; also elsewhere on the board
PA7_TIM3_CH2: R23.1; also elsewhere on the board
PA8_Main_Con_1: Q5.1 (G); also elsewhere on the board
PA10_Brake_On_2: C1.1, R3.2, R10.2; also elsewhere on the board
PAS_HV_Con: Q6.2 (D), Q6.4 (D); also elsewhere on the board
PAS_HV_Con_Ctrl: Q6.1 (G), R121.1, R124.1
PB0_Motor_RPM: C5.1, R15.2, R20.2, R30.1; also elsewhere on the board
PB1_E_Stop_In: C68.1, R111.2, R112.2; also elsewhere on the board
PB2_Pre_Chg_Rly: Q1.1 (G); also elsewhere on the board
PB3_GP_In_1: C4.1, R14.2, R19.2; also elsewhere on the board
PB7_Aux_Supply_Cont: Q8.1 (G); also elsewhere on the board
PC2_PAS_Con: R121.2; also elsewhere on the board
PC3_Brake_Vac_Con: R17.2; also elsewhere on the board
PC4_GP_Out_1: R12.2; also elsewhere on the board
Pre_Chg_Rly: Q1.2 (D), Q1.4 (D); also elsewhere on the board

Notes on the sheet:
Analogue Outputs
12V Digital Inputs
Digital Outputs
Check Resistor Values
Atmega

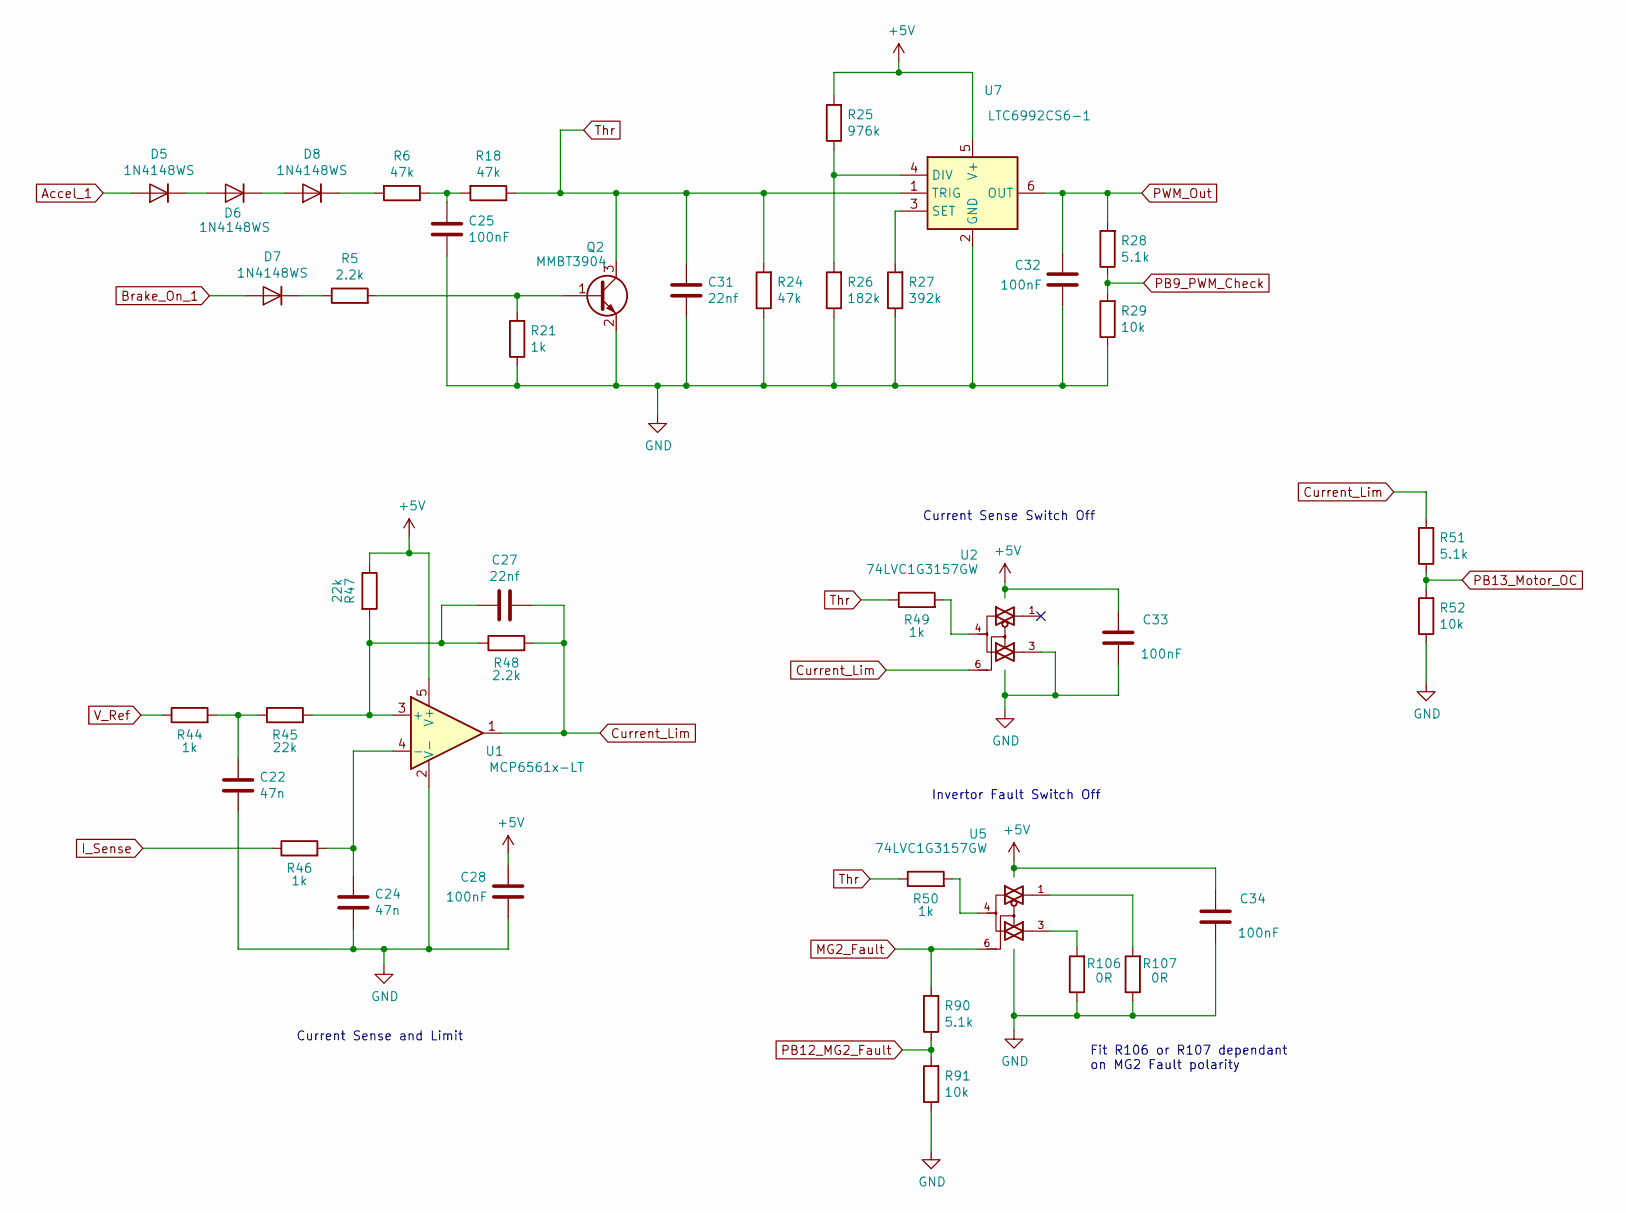
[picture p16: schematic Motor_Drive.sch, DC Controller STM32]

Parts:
C22, C24: 47n; C_0603_1608Metric
C25, C28, C32, C33, C34: 100nF; C_0603_1608Metric
C27, C31: 22nf; C_0603_1608Metric
D5, D6, D7, D8: 1N4148WS; D_SOD-323
Q2: MMBT3904; SOT-23
R5, R48: 2.2k; R_0603_1608Metric
R6, R18, R24: 47k; R_0603_1608Metric
R21, R44, R46, R49, R50: 1k; R_0603_1608Metric
R25: 976k; R_0805_2012Metric
R26: 182k; R_0805_2012Metric
R27: 392k; R_0805_2012Metric
R28, R51, R90: 5.1k; R_0603_1608Metric
R29, R52, R91: 10k; R_0603_1608Metric
R45, R47: 22k; R_0603_1608Metric
R106, R107: 0R; R_0603_1608Metric
U1: MCP6561x-LT; SOT-353_SC-70-5
U2, U5: 74LVC1G3157GW; SOT-363_SC-70-6
U7: LTC6992CS6-1; TSOT-23-6

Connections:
+5V: C28.1, C33.1, C34.1, R25.2, R47.1, U1.5 (V+), U2.5 (VCC), U5.5 (VCC), U7.5 (V+); also elsewhere on the board
Accel_1: D5.2 (A); also elsewhere on the board
Brake_On_1: D7.2 (A); also elsewhere on the board
Current_Lim: C27.1, R48.2, R51.2, U1.1, U2.6
GND: C22.2, C24.2, C25.2, C28.2, C31.2, C32.2, C33.2, C34.2, Q2.2 (E), R21.1, R24.1, R26.1, R27.1, R29.1, R52.1, R91.1, R106.1, R107.1, U1.2 (V-), U2.2 (GND), U2.3, U5.2 (GND), U7.2 (GND); also elsewhere on the board
I_Sense: R46.1; also elsewhere on the board
MG2_Fault: R90.2, U5.6; also elsewhere on the board
unnamed: C22.1, R44.2, R45.1
unnamed: C24.1, R46.2, U1.4 (-)
unnamed: C25.1, R6.1, R18.2
unnamed: C27.2, R45.2, R47.2, R48.1, U1.3 (+)
unnamed: D5.1 (K), D6.2 (A)
unnamed: D6.1 (K), D8.2 (A)
unnamed: D7.1 (K), R5.1
unnamed: D8.1 (K), R6.2
unnamed: Q2.1 (B), R5.2, R21.2
unnamed: R25.1, R26.2, U7.4 (DIV)
unnamed: R27.2, U7.3 (SET)
unnamed: R49.2, U2.4
unnamed: R50.2, U5.4
unnamed: R106.2, U5.3
unnamed: R107.2, U5.1
PB9_PWM_Check: R28.1, R29.2; also elsewhere on the board
PB12_MG2_Fault: R90.1, R91.2; also elsewhere on the board
PB13_Motor_OC: R51.1, R52.2; also elsewhere on the board
PWM_Out: C32.1, R28.2, U7.6 (OUT); also elsewhere on the board
Thr: C31.1, Q2.3 (C), R18.1, R24.2, R49.1, R50.1, U7.1 (TRIG)
V_Ref: R44.1; also elsewhere on the board

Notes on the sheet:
Current Sense and Limit
Current Sense Switch Off
Invertor Fault Switch Off
Fit R106 or R107 dependant on MG2 Fault polarity

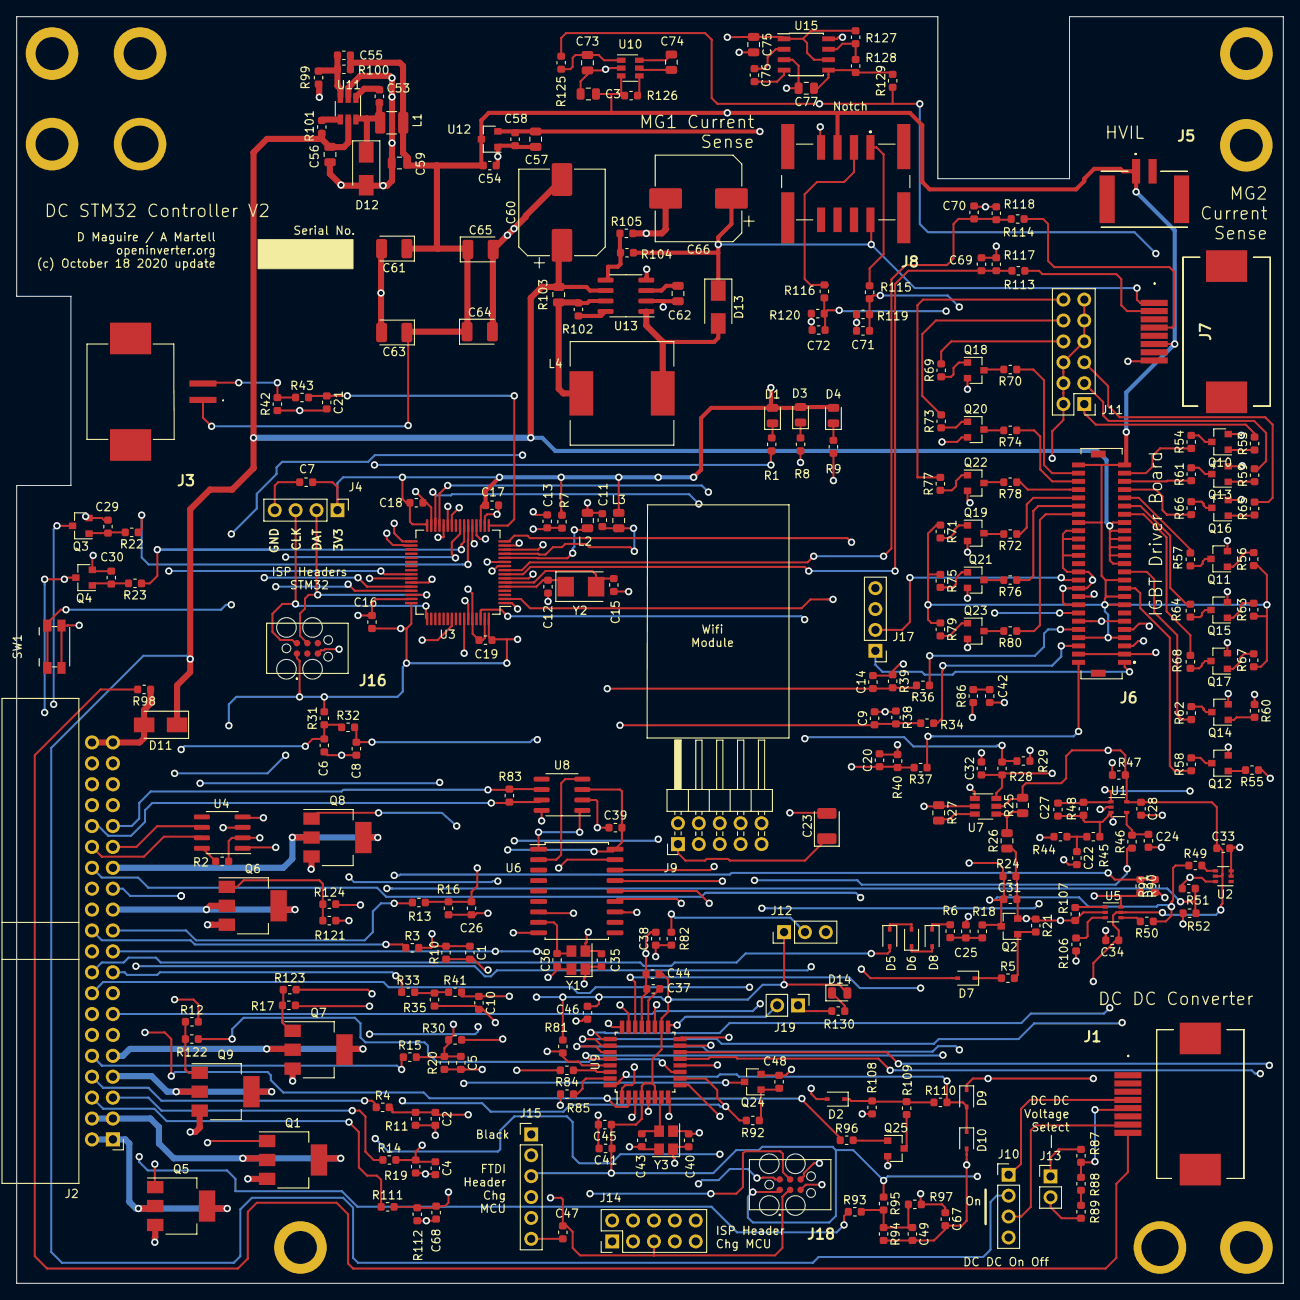
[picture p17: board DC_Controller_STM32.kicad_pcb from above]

Board: 4 copper layers, 154.0 x 154.0 mm, 293 parts (0 on the bottom side), 223 nets.

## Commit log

2020-10-17 Initial commit for manufacture
    [Charger_Control.sch, DC Controller IO.sch, DC Controller Motor Drive.sch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]
2020-10-18 removed SG3204 and TX4313 -5V charge pumps and added LM2776 in their place
    [DC Controller PSU Connectors.sch, DC Controller STM32 v2.kicad_pcb, PSU.sch]
2020-10-18 updated file names to make it easier to use git!
    [Connectors.sch, DC_Controller_STM32.kicad_pcb, DC_Controller_STM32.sch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]
2020-10-18 corrected tracking error around MG1 and MG current sensors. J7 footprint updated (J1 left unchanged as tracking layout is currently ok).
    [Charger_Control.sch, Connectors.sch, DC Controller STM32 v2_bom_2.csv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]
